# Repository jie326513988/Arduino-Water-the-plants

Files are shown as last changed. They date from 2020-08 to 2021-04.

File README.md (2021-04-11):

## 一款迷你型的植物浇水系统，包括代码、电路板原理图PCB图和适用3D打印的外壳
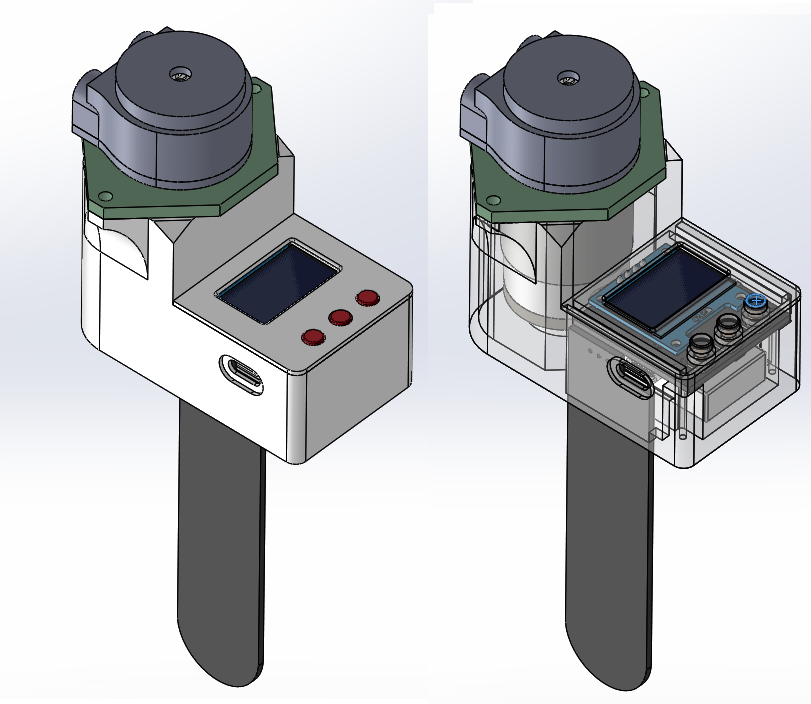
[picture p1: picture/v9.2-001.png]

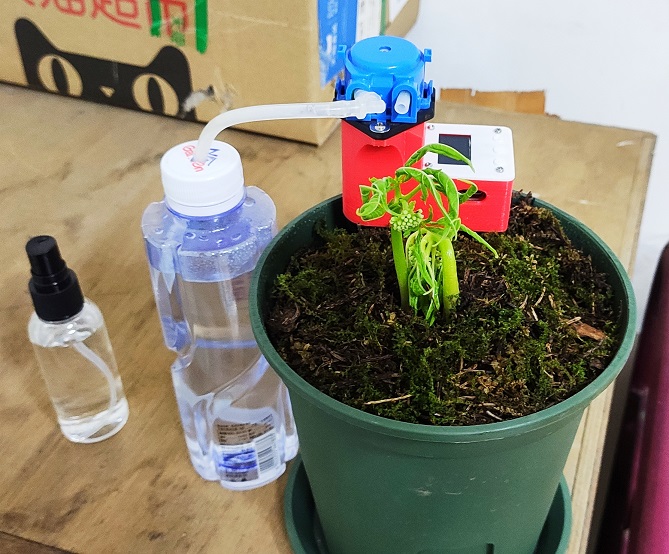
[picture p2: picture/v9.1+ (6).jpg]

#### 注意！所有版本PCB未加到电池低压保护，电池过放会导致电池寿命下降，请使用带保护板的电池，不要让电池电压低于3.0V。
#### 2021-4-11 v1.1.4c版本发布
* 1.修正休眠时间单位显示错误问题
* 2.修改字库位置为本地调用并去除用不上的符号字母
* 3.设置界面添加页码条动画
* 4.美化开机和唤醒检查土湿&电压的检查动画
#### 2021-1-17 LDO版本已验证成功，适合3D打印的外壳已测试成功
## 特点
* 根据自己设定的土壤湿度阈值进行浇水，而不是简单定时浇水，避免不必要的浇水。
* 无浇水任务时自动进入休眠以节省电量，休眠电流0.6ma，满足数周充一次电（小型花盆），配合太阳能充电器可实现长期无人监管。
* MX612E电机驱动芯片，支持pwm调节水泵速度，带过热断电保护。
* 主控PCB+电容式土壤湿度检测PCB的组合结构，主控集成土湿驱动电路，传感器可飞线，也可将从侧面焊接到主控板上，实现更高的集成度。
* 观看视频 https://www.bilibili.com/video/BV1UV411b7vG

## 使用说明（必看）
* 按键1：确认/唤醒，按键2：上/加/左，按键3：下/减/右，按下下键不放再按下确认键即可软重启系统
* 主界面可切换 AUTO/OFF 模式，AUTO模式手动浇水不可用、可自动休眠和唤醒，OFF模式可手动浇水、不会自动休眠和唤醒
* 主控板没有电池低压保护电路，电池过放会导致电池寿命下降，请使用带保护板的电池，不要让电池电压低于3.0V
* 初次使用建议校准参考电压，这样电量显示比较准。测量屏幕的供电电压就是参考电压
* 使用低放电倍率的电池可能会导致水泵启动时触发电池保护板的过流保护而断电，打开水泵平滑启动功能可改善这一现象，原因是有些水泵的启动电流太高导致触发保护，平滑启动可降低水泵的启动电流
* 使用6V蠕动泵，管径越大出水量越多，建议5mm的外径，3mm内径的硅胶管
* 出水口不能离土壤湿度传感器太远，太远湿度传递慢会导致花盆满水溢出
* 浇水速度不能太快，调节PWM MAX即可调节浇水速度，太快会导致只有传感器附近的土是湿的
* 想追求完美的浇水效果的话，需要将土壤湿度传感器水平埋在花盆底部，做好传感器的防水措施就行
* 使用4个M2x12螺丝固定面壳
## 菜单设置说明
* 土壤湿度菜单：设置浇水的上限和下限，启动浇水的延迟时间，停止浇水的延迟时间
* 水泵菜单：设置水泵超时时间（湿度增长率小于4%且持续设定的时间则自动停机休眠），设置水泵是否需要平滑启动，平滑启动的初始PWM值和PWM增量值
* 休眠&亮度菜单：设置休眠时间、亮屏时间、OLED亮度
* 电压&频率菜单：设置电池低压报警值、参考电压值、PWM频率、PWM最大值
* 土湿校准菜单：设置校准土壤湿度的范围，建议暴露在空气中校准为10%，浸泡在水中为95%
* 恢复出厂设置：重置所有参数

## 硬件配置
* 使用500mah，3.7V锂电池供电，休眠耗电0.6ma
* 外接OLED II2模块
* 带充电、升压、LDO电路
* 电机驱动电路
* 带电容式土壤湿度传感器驱动电路   

## 烧录说明
    1.将我提供的库文件放好位置
    2.方法a：使用空芯片，再用AVR ICSP在线烧录器或离线烧录器烧录引导或带引导的固件，之后使用CH340串口模块即可更新程序
      方法b：买一块UNO，上传好程序，将芯片拆下来再焊到浇水板子上
      方法c：使用Arduino uno作为icsp烧录器对空芯片进行烧录引导，再通过CH340上传程序
    3.使用ch340模块更新程序，需要手动复位，打开Arduino IDE，文件-首选项-显示详情输出-上传勾选，点击主界面上传按钮，看到下方出现Overriding Baud Rate: 115200，迅速按下复位按钮即可更新程序
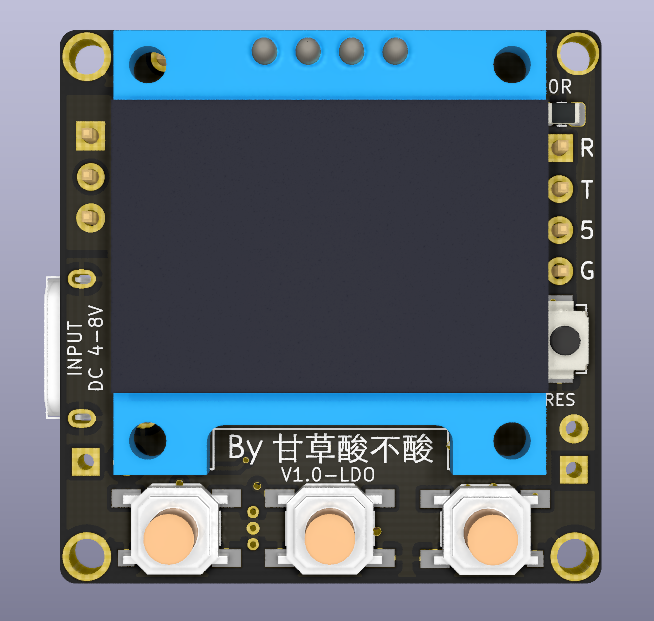
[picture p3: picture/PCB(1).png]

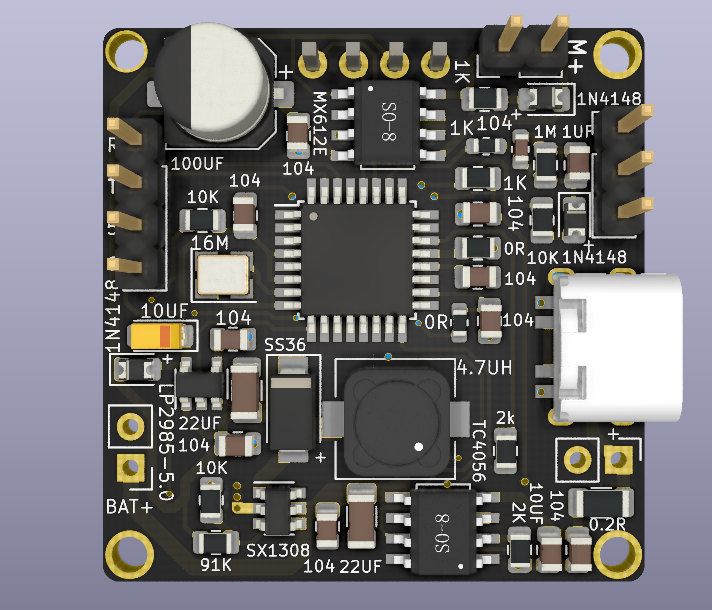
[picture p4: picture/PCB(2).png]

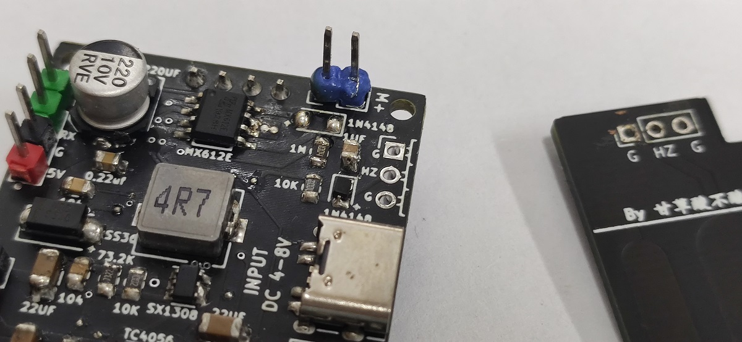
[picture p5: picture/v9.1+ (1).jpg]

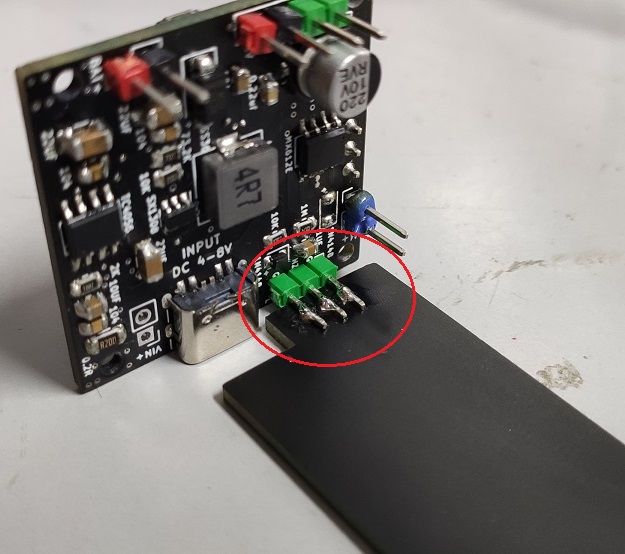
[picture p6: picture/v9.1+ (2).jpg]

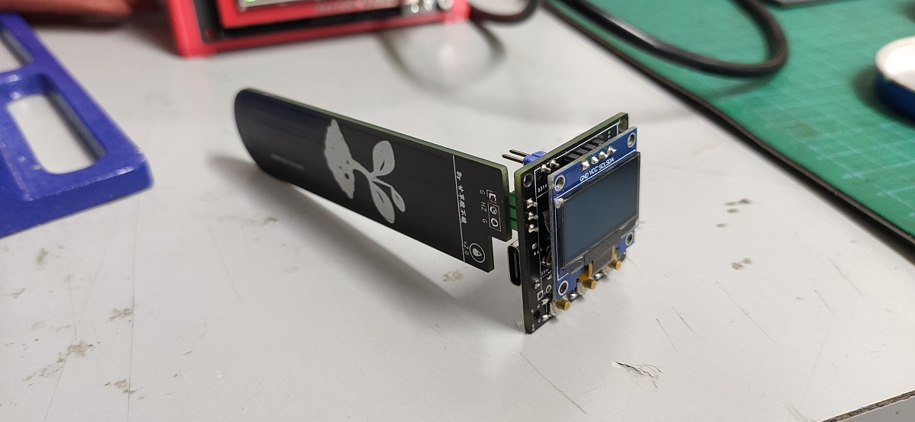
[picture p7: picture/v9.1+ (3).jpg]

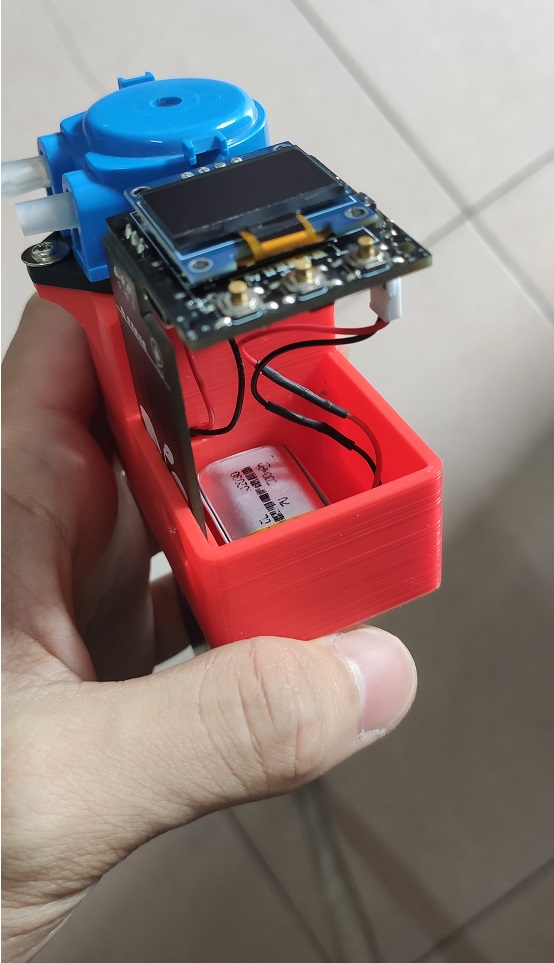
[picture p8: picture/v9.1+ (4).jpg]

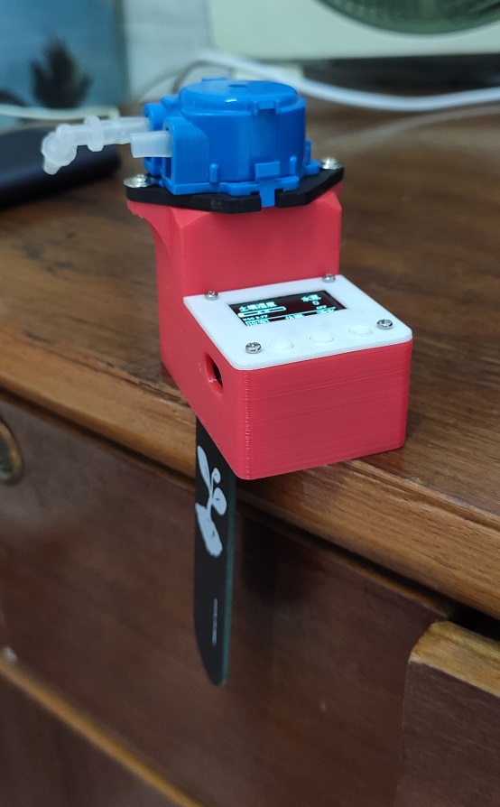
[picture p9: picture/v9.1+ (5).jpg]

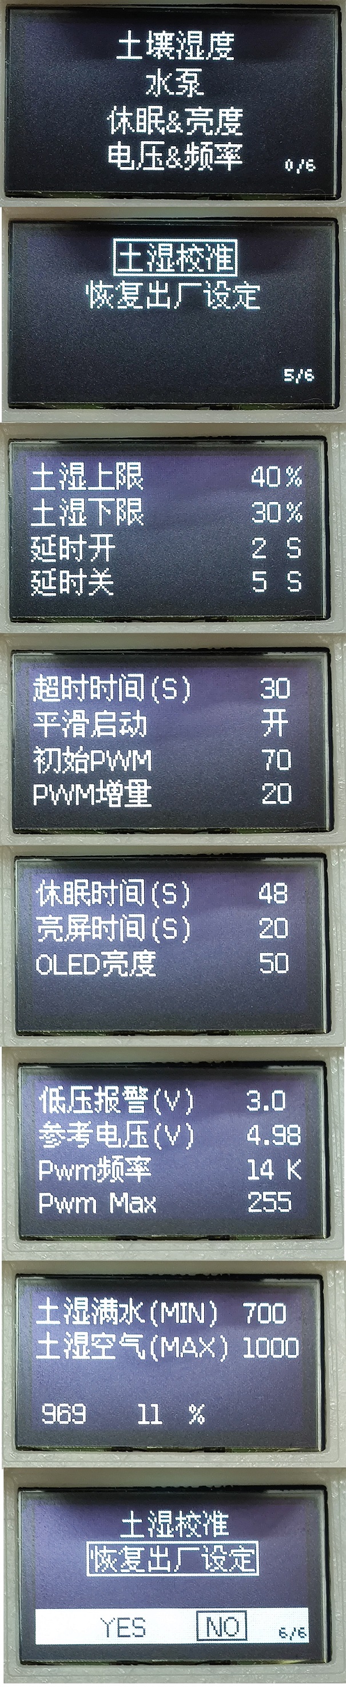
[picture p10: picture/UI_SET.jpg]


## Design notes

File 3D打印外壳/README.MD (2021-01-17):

## 打印件测试完毕，完美配合,仅LDO版本的PCB使用
### 大身的3D打印件有两种，主要区别是oled屏幕的适配
	* 一款是适配薄款的OLED，总厚度为2.7mm左右
	* 一款是适配正常厚度OLED，总厚度为4mm左右

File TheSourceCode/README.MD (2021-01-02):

#### A固件为上古版本V7的适配(L9110适用)
	* 外接土壤湿度传感器
	* L9110电机驱动
#### B固件为V9版本的适配（mx612e适用）
	* 集成土湿驱动电路
	* mx612e电机驱动
	* 无Ldo稳压电路
	* 不太稳定
#### C固件为V1.0-LDO稳定版，即最新版本
	* 集成土湿驱动电路
	* 集成Ldo稳压电路
	* mx612e电机驱动
	* 全新更加稳定的布线

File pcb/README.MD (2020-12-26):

#### 旧版本没有集成Ldo稳压，电机启动的时候纹波太大，导致读取到的土壤湿度会飘
#### 新版本将加入LDO稳压，全局重新布线，以增加电路稳定性
#### 届时新旧版本的代码将不通用

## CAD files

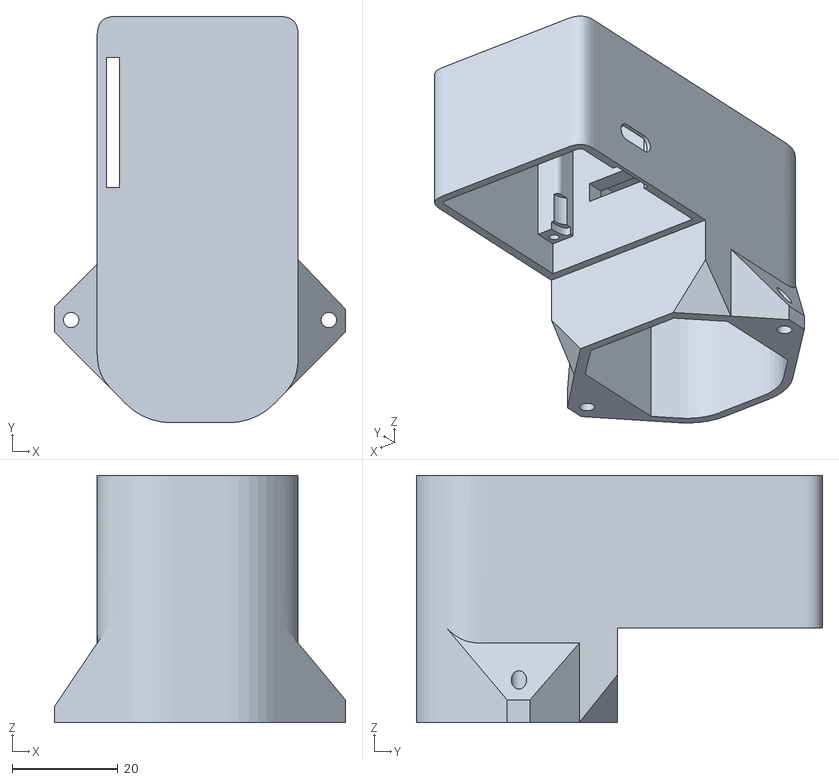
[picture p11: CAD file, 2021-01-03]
3D打印外壳/大身-适配薄款的OLED.STL
55.0 x 76.8 x 46.7

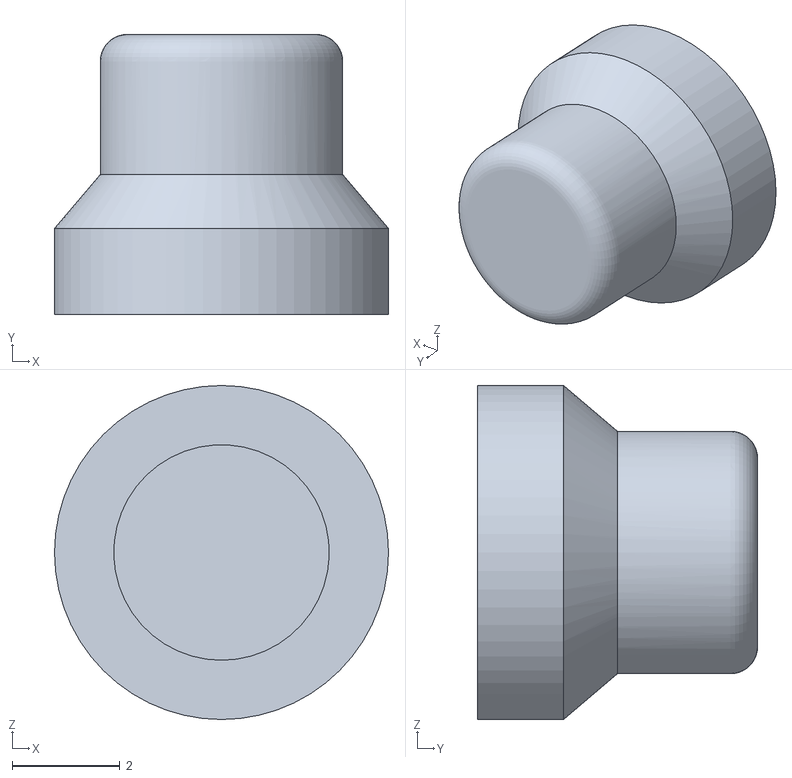
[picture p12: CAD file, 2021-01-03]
3D打印外壳/按键.STL
6.20 x 5.20 x 6.20

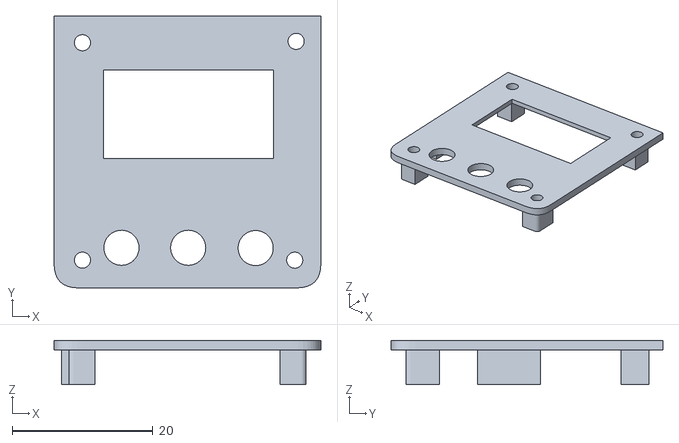
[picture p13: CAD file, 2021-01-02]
3D打印外壳/面盖.STL
38.0 x 38.7 x 6.30

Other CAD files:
3D打印外壳/大身-适配普通款OLED.STL

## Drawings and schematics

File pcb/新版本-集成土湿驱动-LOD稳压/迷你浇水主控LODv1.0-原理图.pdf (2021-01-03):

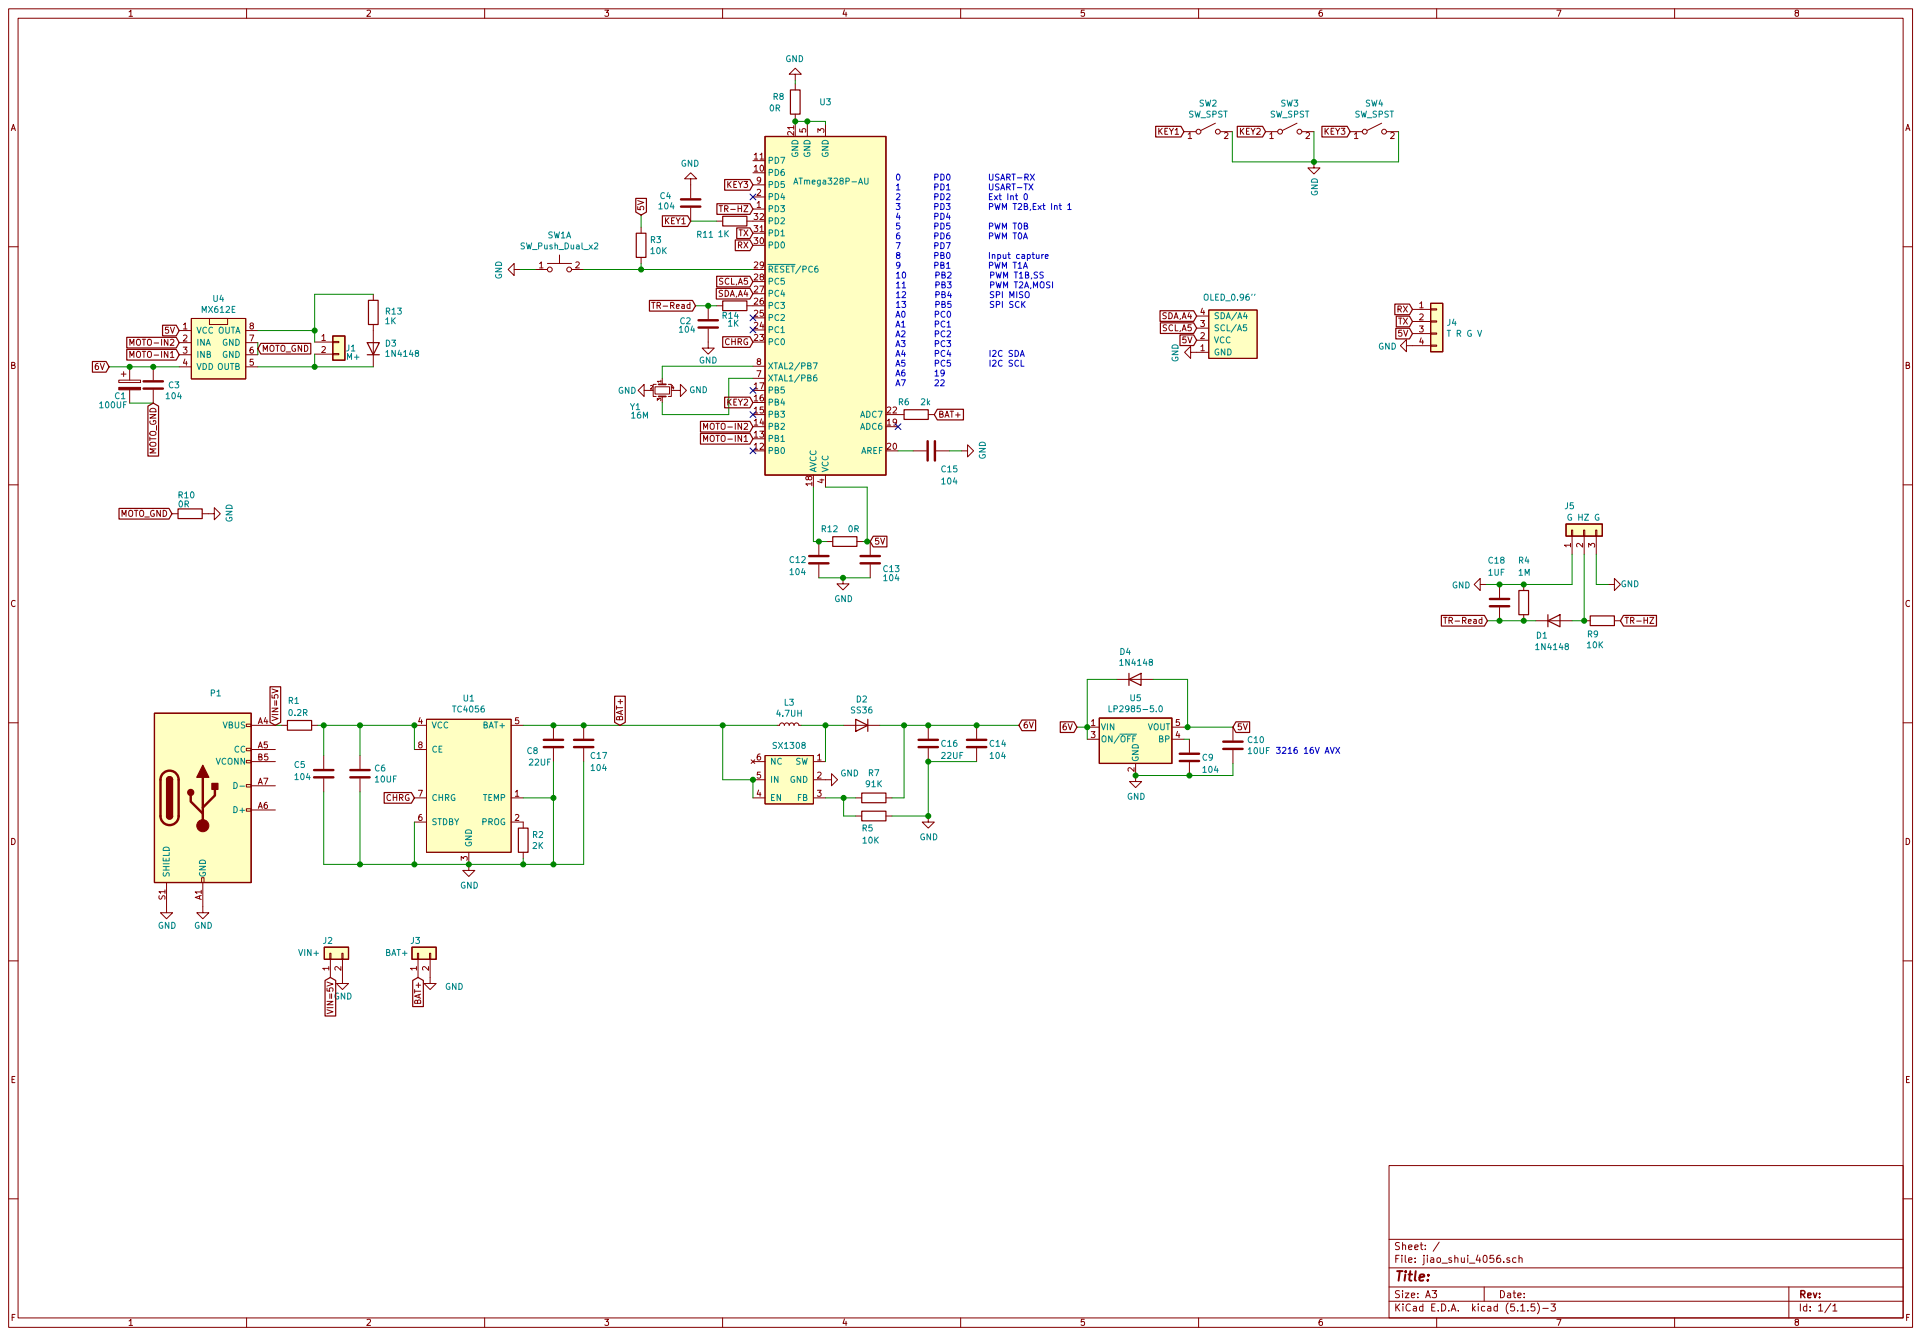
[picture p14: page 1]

BAT+ TR-Read VIN=5V

3 VCC 4 BAT+ 5 STDBY 6 CHRG 7 CE 8 U1 TC4056

2 ON/OFF 3 BP 4 VOUT 5 U5

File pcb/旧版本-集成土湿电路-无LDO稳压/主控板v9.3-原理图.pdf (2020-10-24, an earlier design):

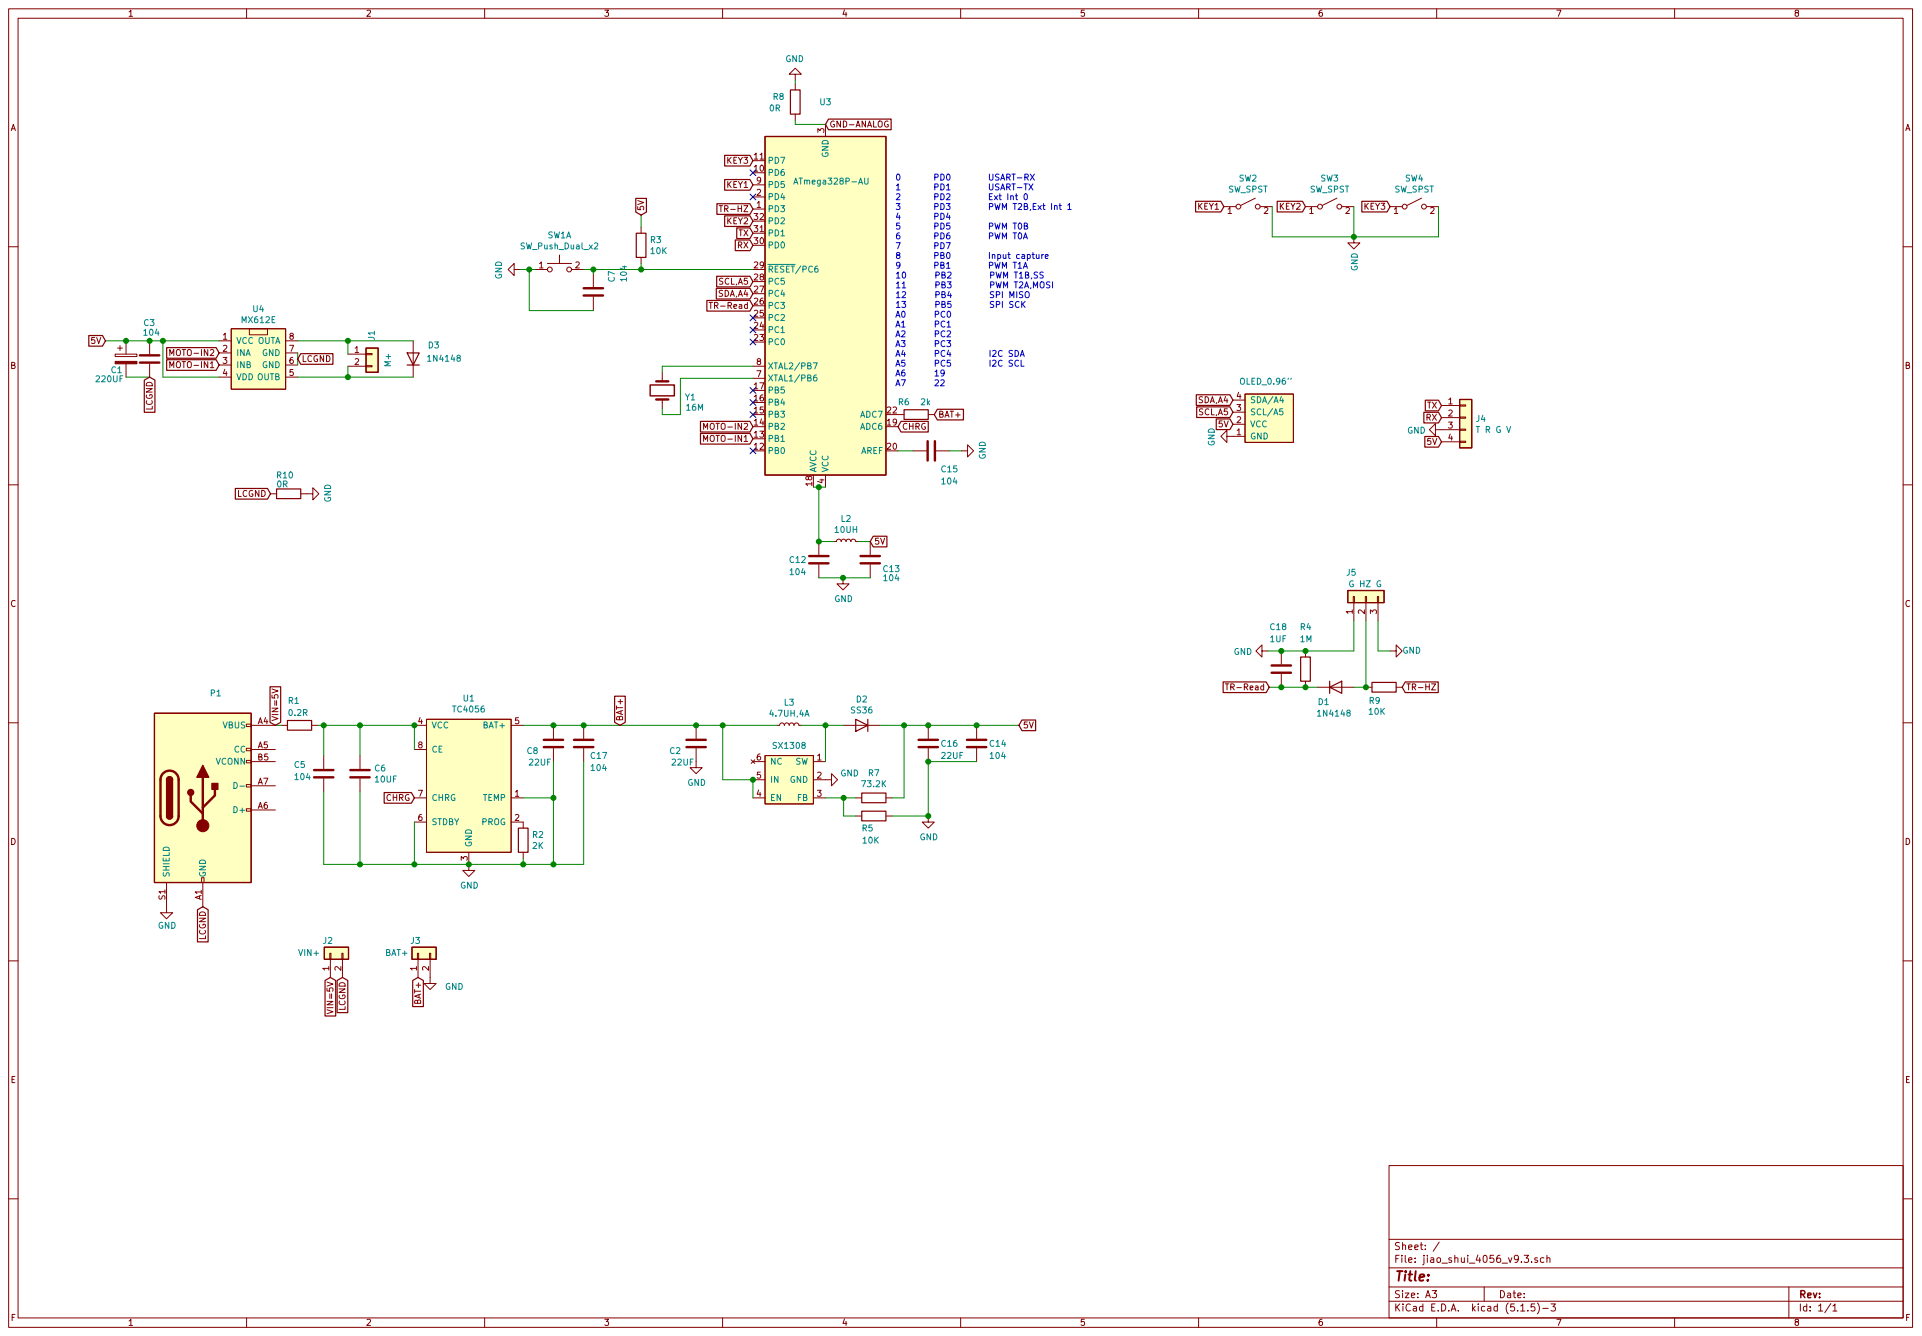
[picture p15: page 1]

3 VCC 4 BAT+ 5 STDBY 6 CHRG 7 CE 8 U1 TC4056 D1

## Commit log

2019-12-04 Create PCB文件
2020-03-11 更新SS36二极管图片
    之前的二极管图片都显示反了，按图放置的话会烧掉SX1306升压芯片
    [v5.1迷你浇水控制器物料清单.xlsx]
2020-03-13 更新新的版本5.1
    二极管丝印图片修正，5.1版本添加47UF的电解电容，降低电机启动造成的供电不足。
    [v5.1迷你浇水控制器物料清单.xlsx]
